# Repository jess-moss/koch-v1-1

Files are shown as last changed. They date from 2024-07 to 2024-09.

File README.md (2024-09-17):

# Low-Cost Robot Arm: Koch v1.1

This page contains the instructions to build a low-cost robot arm. It's an improved version of the original [Alexander Koch's robot](https://github.com/AlexanderKoch-Koch/low_cost_robot) to ease assembly. Thus, we call it Koch v1.1

For the curious reader, here are the most significant changes made:
1. Made small improvements to the hardware model including but not limited to: fixed screw interferences, cleaned up extraneous material, standardized hole sizes, removed screws fastening into plastic, added board platform to leader robot.
2. Added a platform for the leader arm. While not strictly necessary, this platform allows the follower arm to pick objects off the ground which it could not do in the previous configuration.
3. Removed the need for a soldering iron to assemble and for manually adjusting the voltage convertor, by replacing the DC convertor.
4. Added SolidWorks models to make it easier for the community to contribute.
5. Added a wiring diagram.
6. Added assembly video for leader and follower arm with SW animations.

## Assembly Instructions

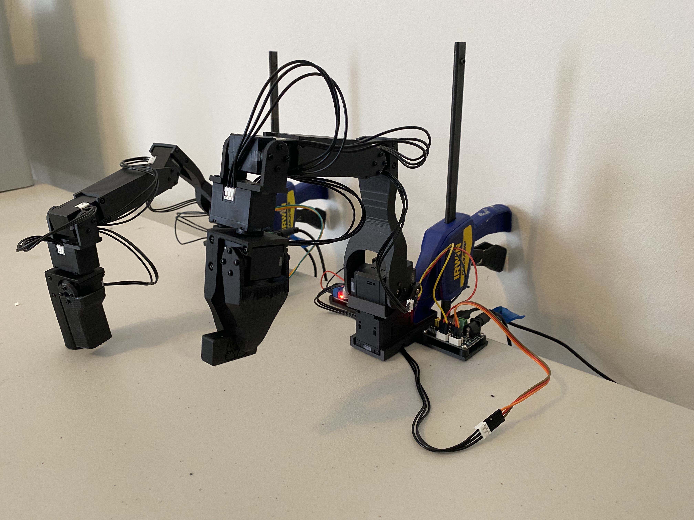
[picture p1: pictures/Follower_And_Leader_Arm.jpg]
Leader And Follower Arm


### Sourcing Parts
Order the off the shelf parts for the leader and follower arm using the links below. Note prices and items may vary slightly depending on geographic location.

#### Leader Arm

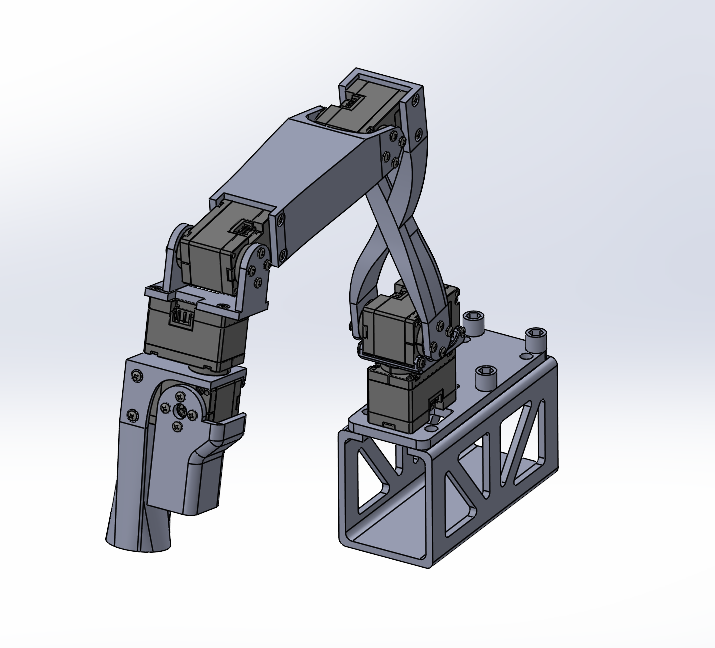
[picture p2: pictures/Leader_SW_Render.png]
Leader Arm


/!\ Warning: We only have links for US, EU, UK, China, and Japan for now. If you find links for other countries like India, please create an issue or PR so that we add them to the list.

| Part | Amount | Unit Cost (US) | Buy US | Unit Cost (EU) | Buy EU | Unit Cost (UK) | Buy UK | Unit Cost (RMB) | Buy CN | Unit Cost (JPY) | Buy JP |
|---|---|---|---|---|---|---|---|---|---|---|---|
| Dynamixel XL330-M077-T | 6 | $24 | [Robotis](https://www.robotis.us/dynamixel-xl330-m077-t) | 40€ | [MyBotShop](https://www.mybotshop.de/DYNAMIXEL-XL330-M077-T)-[GenRobots](https://www.generationrobots.com/en/403818-dynamixel-xl330-m077-t-servo-motor.html) | £27 | [RoboSavvy](https://robosavvy.co.uk/robotis-dynamixel-xl330-m077-t.html) | ¥255 | [TaoBao](https://item.taobao.com/item.htm?id=651202518645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.) | ¥4,070 | [Robotis](https://e-shop.robotis.co.jp/product.php?id=416) |
| XL330 Frame and Idler Wheel 4pcs set<sup>[1](#myfootnote1)</sup> |  1 | $10 | [Robotis](https://www.robotis.us/fpx330-h101-4pcs-set) | 12€ | [MyBotShop](https://www.mybotshop.de/DYNAMIXEL-FPX330-H101-4PCS-Set)-[GenRobots](https://www.generationrobots.com/en/403860-FPX330-H101-hinge-frame-and-idler-set-dynamixel-xl330.html) | £10 |  [RoboSavvy](https://robosavvy.co.uk/fpx330-h101-4pcs-set.html) | ¥100 | [TaoBao](https://item.taobao.com/item.htm?id=646782958666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..) | ¥2,024 | [Robotis](https://e-shop.robotis.co.jp/product.php?id=437) |
| Waveshare Serial Bus Servo Driver Board | 1 | $10 | [Amazon](https://a.co/d/7C3RUYU) | 6€ | [Eckstein](https://eckstein-shop.de/WaveShare-Serial-Bus-Servo-Driver-Board-for-ST-SC-Serial-Bus-Servos-EN) | £11 | [Amazon](https://www.amazon.co.uk/Waveshare-Integrates-Control-Applicable-Integrate/dp/B0CJ6TP3TP/)| ¥24 | [TaoBao](https://item.taobao.com/item.htm?id=739743280684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) | n/a | n/a |
| 5V Power Supply | 1 | $6 | [Amazon](https://a.co/d/5u90NVp) | 9€ | [Amazon](https://www.amazon.fr/LEYF-Alimentation-Universelle-Adaptateur-Enfichable/dp/B09NGVWBSY) | £10 | [Amazon](https://www.amazon.co.uk/Adapter-Switching-100-240V-5-5x2-1mm-Transformer-5V2A-UKCA/dp/B0CH6HFVTK/)| ¥10 | [TaoBao](https://detail.tmall.com/item.htm?id=662655385028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) | ¥899 | [Amazon](https://a.co/d/5u90NVp) |
| Jumper Wires 3*40 pcs set (M-M, M-F, F-F) | 1 | $7 | [Amazon](https://a.co/d/hQfk2cb) | 9€ | [Amazon](https://www.amazon.fr/dp/B0BRMKX5RT/) | £5 | [Amazon](https://www.amazon.co.uk/dp/B09KGRM98K/)| ¥10 | [TaoBao](https://detail.tmall.com/item.htm?id=608543275703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) | n/a | n/a |
| Table Clamp | 1 | $6 | [Amazon](https://a.co/d/4KEiYdV) | n/a | n/a | £14 | [Amazon](https://www.amazon.co.uk/BESSEY-TOOLS-CM30-Forged-C-Clamp/dp/B0006694I2/?th=1)| ¥8 | [TaoBao](https://detail.tmall.com/item.htm?id=597606333219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..) | n/a | n/a |
| Table Clamp 4pcs set<sup>[2](#myfootnote2)</sup> | 1 | n/a | n/a | 14€ | [Amazon](https://www.amazon.fr/CAUTIOUS-Serre-Joint-R%C3%A9glable-Serre-Joints/dp/B0CJMB3SKH) | n/a | n/a | n/a | n/a | n/a | n/a |
| 1.5mm Star/Cruciform Screwdriver 2pcs set | 1 |  $7 | [Amazon](https://www.amazon.com/HARFINGTON-Precision-Screwdriver-Eyeglasses-Electronic/dp/B0D3XQ97XM/?th=1)| 7€ | [Amazon](https://www.amazon.fr/sourcing-map-Cruciforme-%C3%89lectroniques-R%C3%A9paration/dp/B0BQ69J2QF) | £4 | [Amazon](https://www.amazon.co.uk/sourcing-map-Screwdriver-Eyeglasses-Electronics/dp/B0BLM2Y2Z5/) | ¥2 | [TaoBao](https://detail.tmall.com/item.htm?id=790258857614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) | n/a | n/a |
| USB C-A or C-C 2pcs set<sup>[3](#myfootnote3)</sup> | 1 | $9 | [Amazon](https://www.amazon.com/Charging-etguuds-Charger-Braided-Compatible/dp/B0B8NWLLW2/) | 8€ | [Amazon](https://www.amazon.fr/dp/B08J7PQGD7/) | £6 | [Amazon](https://www.amazon.co.uk/Anker-Charger-Braided-Standard-Charging/dp/B07DD5YHMH/)| ¥12 | [TaoBao](https://detail.tmall.com/item.htm?id=44425281296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) | n/a | n/a |
| Total | | $199 | | 305€ | | £222 | | ¥1696 | | ¥6993 | |

#### Follower Arm

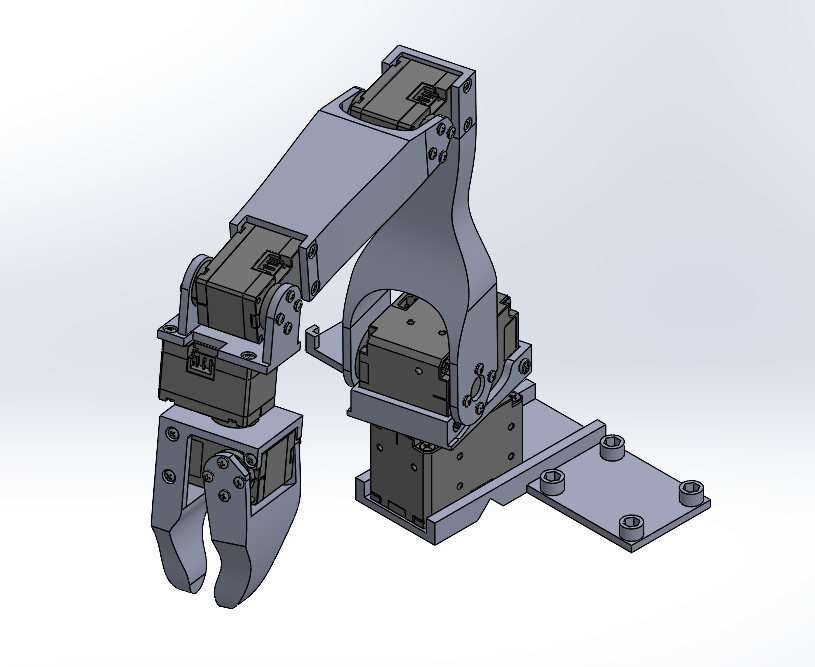
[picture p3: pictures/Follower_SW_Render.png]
Follower Arm


/!\ Warning: We only have links for US, EU, UK, China, and Japan for now. If you find links for other countries like India, please create an issue or PR so that we add them to the list.

| Part | Amount | Unit Cost (US) | Buy US | Unit Cost (EU) | Buy EU | Unit Cost (UK) | Buy UK | Unit Cost (RMB) | Buy CN | Unit Cost (JPY) | Buy JP
|---|---|---|---|---|---|---|---|---|---|---|---|
| Dynamixel XL430-W250-T |  2 | $50 | [Robotis](https://www.robotis.us/dynamixel-xl430-w250-t) | 57-61€ | [MyBotShop](https://www.mybotshop.de/DYNAMIXEL-XL430-W250-T)-[GenRobots](https://www.generationrobots.com/en/402823-dynamixel-xl430-w250-t-servomotor.html) | £47 | [RoboSavvy](https://robosavvy.co.uk/dynamixel-xl430-w250-t.html) | ¥485 | [TaoBao](https://item.taobao.com/item.htm?id=588178867677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) | ¥6,831 | [Robotis](https://e-shop.robotis.co.jp/product.php?id=40)
| Dynamixel XL330-M288-T |  4 | $24  | [Robotis](https://www.robotis.us/dynamixel-xl330-m288-t) | 40-46€ | [MyBotShop](https://www.mybotshop.de/DYNAMIXEL-XL330-M288-T)-[GenRobots](https://www.generationrobots.com/en/403817-dynamixel-xl330-m288-t-servo-motor.html) | £27 | [RoboSavvy](https://robosavvy.co.uk/robotis-dynamixel-xl330-m288-t.html) | ¥255 | [TaoBao](https://item.taobao.com/item.htm?id=648175925849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) | ¥4,070 | [Robotis](https://e-shop.robotis.co.jp/product.php?id=417)
| XL330 Frame and Idler Wheel 4pcs set<sup>[1](#myfootnote1)</sup> |  1 | $10 | [Robotis](https://www.robotis.us/fpx330-h101-4pcs-set) | 12€ | [MyBotShop](https://www.mybotshop.de/DYNAMIXEL-FPX330-H101-4PCS-Set)-[GenRobots](https://www.generationrobots.com/en/403860-FPX330-H101-hinge-frame-and-idler-set-dynamixel-xl330.html) | £10 |  [RoboSavvy](https://robosavvy.co.uk/fpx330-h101-4pcs-set.html) | ¥100 | [TaoBao](https://item.taobao.com/item.htm?id=646782958666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..) | ¥2,024 | [Robotis](https://e-shop.robotis.co.jp/product.php?id=437) |
| XL430 Idler Wheel set | 1 | $7 | [Robotis](https://www.robotis.us/hn11-i101-set) | 9€ | [MyBotShop](https://www.mybotshop.de/DYNAMIXEL-XL430-HN11-I101-Set)-[GenRobots](https://www.generationrobots.com/en/403206-hn11-i101-horn-set.html) | £7 | [Robosavvy](https://robosavvy.co.uk/hn11-i101-set.html)| ¥75 | [TaoBao](https://item.taobao.com/item.htm?id=581922883001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..) | ¥836 | [Robotis](https://e-shop.robotis.co.jp/product.php?id=147)
| Waveshare Serial Bus Servo Driver Board | 1 | $10 | [Amazon](https://a.co/d/7C3RUYU) | 6€ | [Eckstein](https://eckstein-shop.de/WaveShare-Serial-Bus-Servo-Driver-Board-for-ST-SC-Serial-Bus-Servos-EN) | £11 | [Amazon](https://www.amazon.co.uk/Waveshare-Integrates-Control-Applicable-Integrate/dp/B0CJ6TP3TP/)| ¥24 | [TaoBao](https://item.taobao.com/item.htm?id=739743280684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) | n/a | n/a |
| Voltage Reducer | 1 | $14 | [Amazon](https://www.amazon.com/EPLZON-Converter-5V-5-3V-Transformer-Regulator/dp/B09R4DBZJK) | 14€ | [Amazon](https://www.amazon.fr/dp/B0B58T2YY8/) | £15 | [Amazon](https://www.amazon.co.uk/Converter-Voltage-Regulator-Transformer-Charging/dp/B0989DKYWN) | ¥11 | [TaoBao](https://detail.tmall.com/item.htm?id=617425895508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) | n/a | n/a |
| 12V Power Supply | 1 | $12 | [Amazon](https://a.co/d/40o8uMN) | 15-36€ | [Amazon](https://www.amazon.fr/LEDMO-Alimentation-Adaptateur-Transformateurs-Chargeur/dp/B07PGLXK4X)-[GenRobots](https://www.generationrobots.com/en/400866-smps-charger-for-bioloid-and-dynamixel-robotis.html) | £13 | [Amazon](https://www.amazon.co.uk/Facmogu-Adapter-100-240V-Monitors-Amplifier/dp/B0CXPMJJMF/) | ¥20 | [TaoBao](https://detail.tmall.com/item.htm?id=678305663026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) | ¥1,685 | [Amazon](https://a.co/d/40o8uMN) |
| Jumper Wires 3*40 pcs set (M-M, M-F, F-F) | 1 | $7 | [Amazon](https://a.co/d/hQfk2cb) | 9€ | [Amazon](https://www.amazon.fr/dp/B0BRMKX5RT/) | £5 | [Amazon](https://www.amazon.co.uk/dp/B09KGRM98K/)| ¥10 | [TaoBao](https://detail.tmall.com/item.htm?id=608543275703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) | n/a | n/a |
| Table Clamp | 1 | $6 | [Amazon](https://a.co/d/4KEiYdV) | n/a | n/a | £14 | [Amazon](https://www.amazon.co.uk/BESSEY-TOOLS-CM30-Forged-C-Clamp/dp/B0006694I2/?th=1) | ¥8 | [TaoBao](https://detail.tmall.com/item.htm?id=597606333219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..) | n/a | n/a |
| Table Clamp 4pcs set<sup>[4](#myfootnote4)</sup> | 1 | n/a | n/a | 14€ | [Amazon](https://www.amazon.fr/CAUTIOUS-Serre-Joint-R%C3%A9glable-Serre-Joints/dp/B0CJMB3SKH) | n/a | n/a | n/a | n/a | n/a | n/a |
| 1.5mm Star/Cruciform Screwdriver 2pcs set<sup>[4](#myfootnote5)</sup> | 1 |  $7 | [Amazon](https://www.amazon.com/HARFINGTON-Precision-Screwdriver-Eyeglasses-Electronic/dp/B0D3XQ97XM/?th=1)| 7€ | [Amazon](https://www.amazon.fr/sourcing-map-Cruciforme-%C3%89lectroniques-R%C3%A9paration/dp/B0BQ69J2QF) | £4 | [Amazon](https://www.amazon.co.uk/sourcing-map-Screwdriver-Eyeglasses-Electronics/dp/B0BLM2Y2Z5/) | ¥2 | [TaoBao](https://detail.tmall.com/item.htm?id=790258857614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) | n/a | n/a |
| USB C-A or C-C 2pcs set<sup>[6](#myfootnote6)</sup> | 1 | $9 | [Amazon](https://www.amazon.com/Charging-etguuds-Charger-Braided-Compatible/dp/B0B8NWLLW2/) | 8€ | [Amazon](https://www.amazon.fr/dp/B08J7PQGD7/) | £6 | [Amazon](https://www.amazon.co.uk/Anker-Charger-Braided-Standard-Charging/dp/B07DD5YHMH/)| ¥12 | [TaoBao](https://detail.tmall.com/item.htm?id=44425281296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) | n/a | n/a |
| Total | | $278 | | 368€ | | £285 | | ¥2251 | | ¥15446 | |

### Printing the Parts
A variety of 3D printers are acceptable to print the parts necessary of the follower and leader arm. Follow the steps below to ensure a good print.

1. Choose a printer: When choosing a printer there are a variety of factors to consider. Below are the suggested printed settings, although using a printer outside these parameters may likely work as well.
   1. Precision: 0.2mm minimum height layer<sup>[7](#myfootnote7)</sup>
   2. Material: PLA+, ABS, PETG or other reasonably strong plastics.
   3. Nozzle Diameter: 0.4mm maximum nozzle diameter
   4. Infill Density: ~30% <sup>[8](#myfootnote8)</sup>
   5. Sample Printers: [Prusa Mini+](https://www.prusa3d.com/product/original-prusa-mini-semi-assembled-3d-printer-4/), [Bambu P1](https://us.store.bambulab.com/collections/p1-series/products/p1p), [Ender3](https://www.amazon.com/Comgrow-Creality-Ender-Aluminum-220x220x250mm/dp/B07BR3F9N6/), etc.  
2. Set up the printer
   1. Materials:<sup>[9](#myfootnote9)</sup>
      1. [Standard Glue Stick](https://www.amazon.com/Amazon-Basics-Washable-School-Sticks/dp/B0CRCWCGNW/)
      2. [Putty Knife](https://www.amazon.com/Warner-ProGrip-Putty-Knife-90133/dp/B000I1VEK6/)
   2. Setup and Takedown
      1. Ensure that the printer is calibrated and the bed level is correctly set using the printer specific instructions.
      2. Clean the print bed, making sure it is free from dust, or grease. If cleaning the bed using water, or other liquid, dry the bed.
      3. Use a standard glue stick and apply a thin, even layer of glue across the print area of the bed. Avoid clumping or uneven application.
      4. Load the printer filament using printer specific instructions.
      5. Ensure the printer settings match the ones suggested above (most printers have multiple settings so choose the ones that most closely match).
      6. Check file type, choose the file(s) from the hardware folder and print.<sup>[10](#myfootnote10)</sup>
3. Print one of each of parts found in `hardware/leader/STL` and `hardware/follower/STL`, which are listed below.
   1. Leader:
      1. Leader_Base
      2. Leader_Elbow_To_Wrist
      3. Leader_Elbow_To_Wrist_Extension
      4. Leader_Gripper_Handle
      5. Leader_Gripper_Trigger
      6. Leader_Shoulder_To_Elbow
      7. Leader_Platform<sup>[11](#myfootnote11)</sup>
      8. Robotis_FPX330_S101<sup>[12](#myfootnote12)</sup>
   2. Follower:
      1. Follower_Base
      2. Follower_Elbow_To_Wrist
      3. Follower_Elbow_To_Wrist_Extension
      4. Follower_Gripper_Moving_Part
      5. Follower_Gripper_Static_Part
      6. Follower_Shoulder_Rotation
      7. Follower_Shoulder_To_Elbow
   3. Optional Parts:<sup>[13](#myfootnote13)</sup>
      1. HuggingFace_Block
      2. LeRobot_Block
4. Take Down
   1. After the print is done, use the putty knife to scrape the the parts off the print bed.
   2. Remove any support material from parts.
   3. Reapply the glue stick before starting the next print.

### Assembling the Parts
Construct the leader and follower arms using the Assembly Video linked below. After you assemble the two arms from the video, power the leader arm using the 5V power supply<sup>[14](#myfootnote14)</sup>, and the follower arm using the 12V power supply. In addition, plug each arm into your computer using a USB-C cable.

Video of the Assembly: [Youtube](https://www.youtube.com/watch?v=8nQIg9BwwTk)

Note: The Leader Platform has been altered to be fastened instead of snapping into place, as the latter design was not creating a tight fit for certain printers. In time, this will be fixed in the video link above, but for now follow the below directions. 

Insert the nuts into the pockets on the underside of the Leader Platform. Then, use the M2x5 machine screws to fasten the Leader_Platform to the Leader_Base. You will need to temporarily remove the Waveshare Serial Bus Servo Driver Board to access the two fasteners beneath it.

Parts:
1. Leader_Platform
2. Four M2x5 Machine Screws
3. Four M2 Nuts

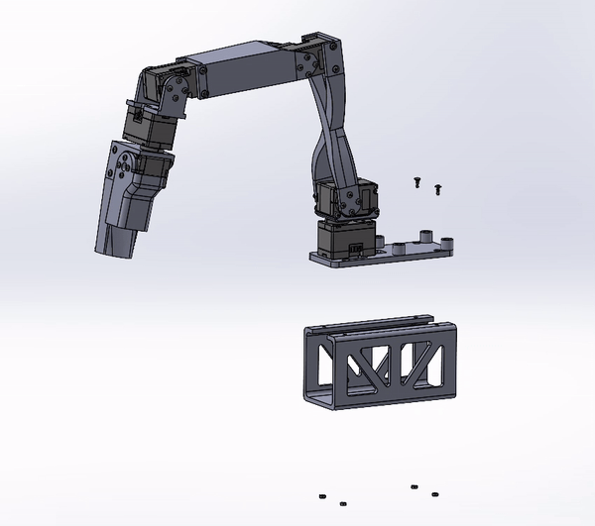
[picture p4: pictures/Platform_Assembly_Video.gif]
Platform Video


### Configure
While this robot can be programmed in a variety of manners, it is suggested to use with [LeRobot](https://github.com/huggingface/lerobot/blob/main/examples/7_get_started_with_real_robot.md).

### Footnotes
<a name="myfootnote1">1</a>: You will only use three idler wheels that come in this four piece set.\
<a name="myfootnote2">2</a>: You will only need one clamp in this four piece set.\
<a name="myfootnote3">3</a>: You will only need one chord in this two piece set. \
<a name="myfootnote4">4</a>: If you bought the 4 piece clamp set for the leader arm, you will not need to buy it again here, as only one clamp is necessary of the follower arm, and one for the leader arm.\
<a name="myfootnote5">5</a>: If you bought the screwdriver set for the leader arm, you will not need to buy it again here as the same screwdriver is used for the follower and leader arm.\
<a name="myfootnote6">6</a>: If you bought the two piece cable set for the leader arm, you will not need to buy it again here, as only one cable is necessary for the leader arm, and one for the follower arm. \
<a name="myfootnote7">7</a>: This precision is based on the fact the through holes for M2 fasteners are 2.4mm in diameter while the nominal diameter of a M2 fastener is 2mm. In a worst case scenario, this allows +/- 0.2mm while still allowing for screw alignment. However, if you are only capable of printing with a larger layer height, you will likely be fine, just ensure the screw holes align as expected.\
<a name="myfootnote8">8</a>: It is quite possible a lower density infill could be used, however, erring on the side of caution, I used 37% to ensure strong parts.  \
<a name="myfootnote9">9</a>: You do not need to buy these exact parts, but a glue stick and putty knife are almost always necessary for a good 3D print. The glue prevents parts from sticking to the print bed, and the putty knife helps scrape parts from the print bed. However, feel free to check with your specific printer instructions for if these parts are necessary. \
<a name="myfootnote10">10</a>: All the printers suggested will print STL files. However, if your printer only prints a different format, ensure you convert the file to the correct extension before printing. \
<a name="myfootnote11">11</a>: This is not strictly necessary to print but does allow the follower arm to reach the ground which is is otherwise unable to do in the current setup. \
<a name="myfootnote12">12</a>: You can either buy the Robotis [FPX330-S101](https://www.robotis.us/fpx330-s101-4pcs-set/), or 3D print it, but it is cheaper to print. \
<a name="myfootnote13">13</a>: Two blocks each the same size as a 2x4 Lego block, not necessary to print, but useful as a starting manipuland. \
<a name="myfootnote14">14</a>: The observant technician may realize the Serial Bus Servo Driver Board suggests an input DC voltage between 9 to 12.6V, where for the leader arm we are only applying 5V. This lower voltage will not hurt the board, and must be done to correctly power the servos on the leader arm.

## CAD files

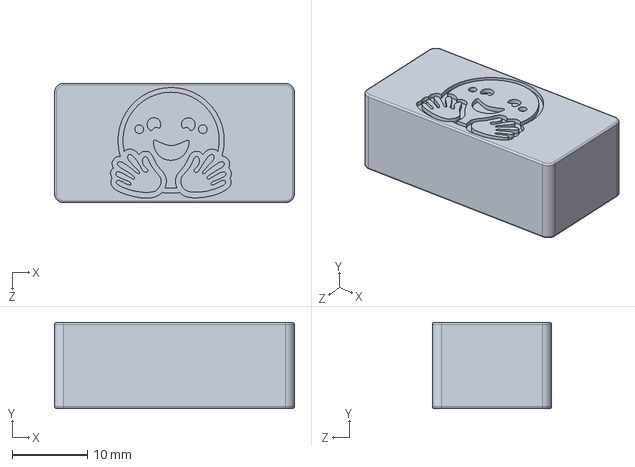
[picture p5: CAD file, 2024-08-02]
hardware/extras/SolidWorks/HuggingFace_Block.SLDPRT
31.8 x 11.4 x 15.8 mm

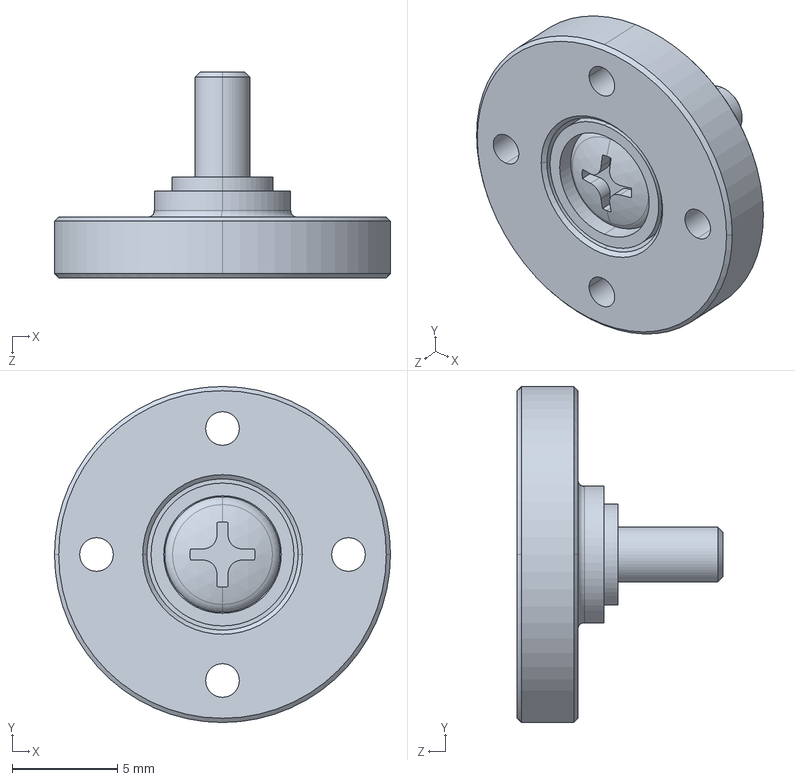
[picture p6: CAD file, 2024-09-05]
hardware/follower/STEP/Robotis_FPX330_H101.STEP
16.0 x 16.0 x 9.80 mm

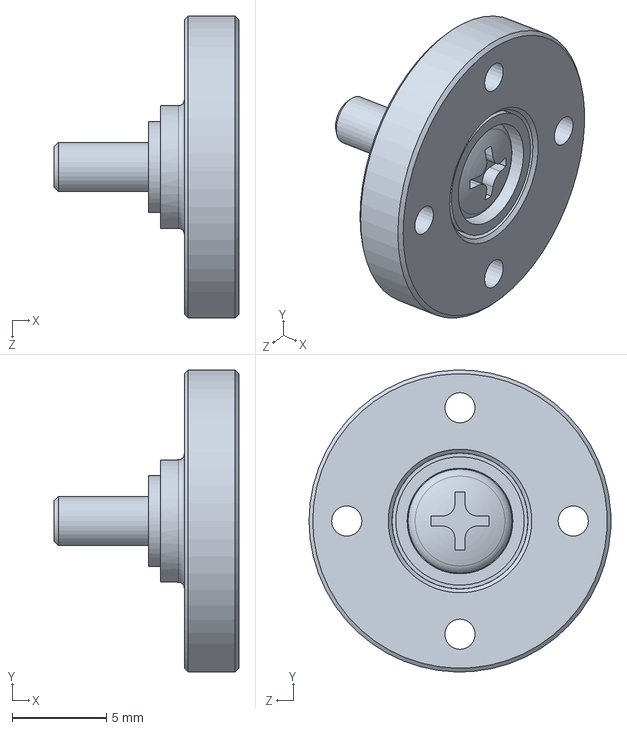
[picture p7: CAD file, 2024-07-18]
hardware/leader/SolidWorks/Robotis_FPX330_H101.SLDPRT
9.80 x 16.0 x 16.0 mm

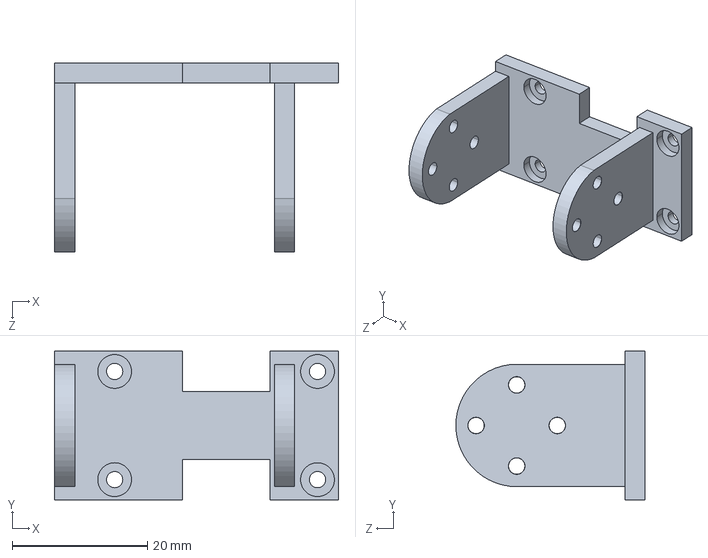
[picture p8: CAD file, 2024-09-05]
hardware/leader/STEP/Leader_Elbow_To_Wrist.STEP
42.0 x 22.0 x 28.0 mm

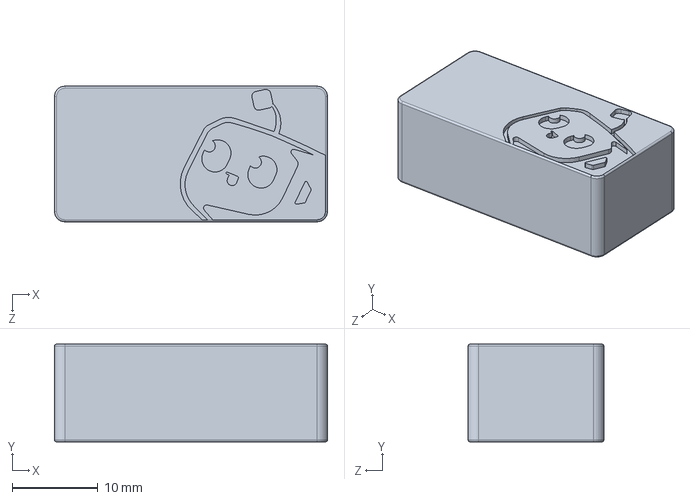
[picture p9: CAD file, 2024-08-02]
hardware/extras/SolidWorks/LeRobot_Block.SLDPRT
31.8 x 11.4 x 15.8 mm

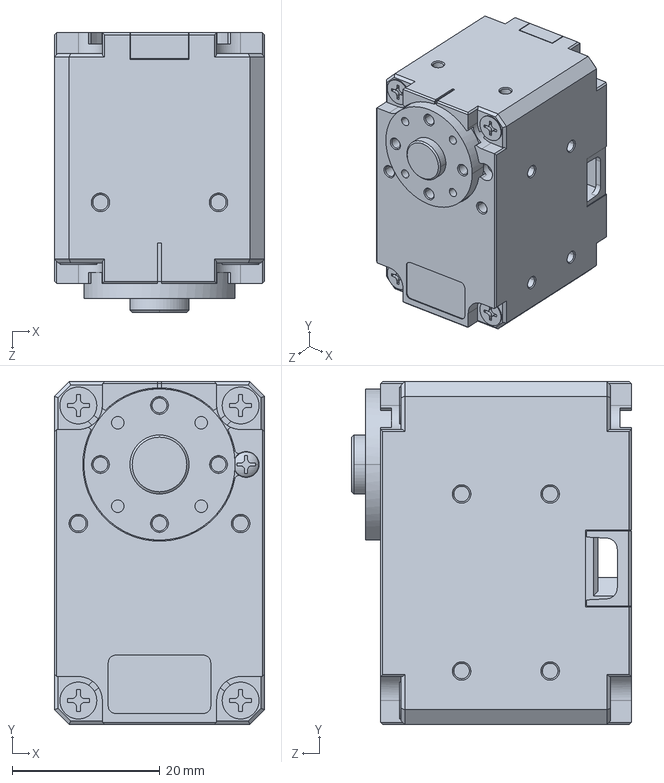
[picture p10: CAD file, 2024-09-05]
hardware/follower/STEP/Robotis_DYNAMIXEL_XL430_W250_T.STEP
28.5 x 46.5 x 37.9 mm

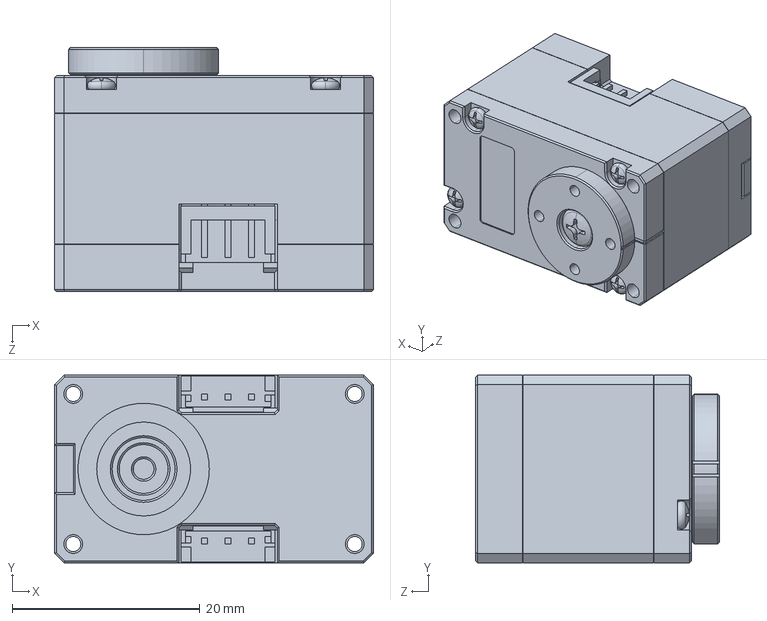
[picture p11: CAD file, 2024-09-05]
hardware/follower/STEP/Robotis_DYNAMIXEL_XL330_M288_T.STEP
34.0 x 20.0 x 26.0 mm

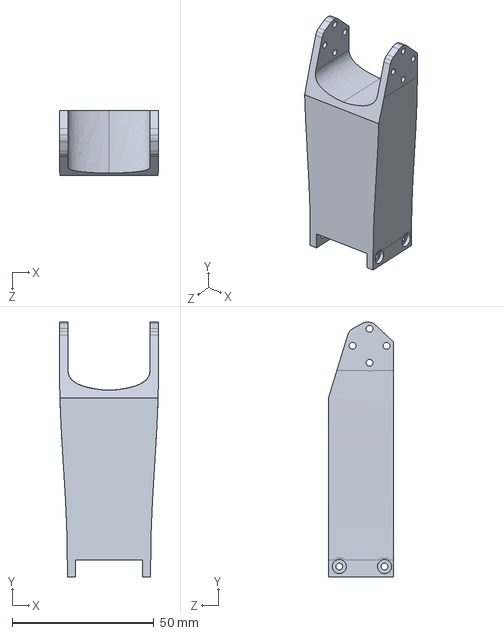
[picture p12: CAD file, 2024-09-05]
hardware/leader/STEP/Leader_Elbow_To_Wrist_Extension.STEP
35.0 x 90.1 x 23.0 mm

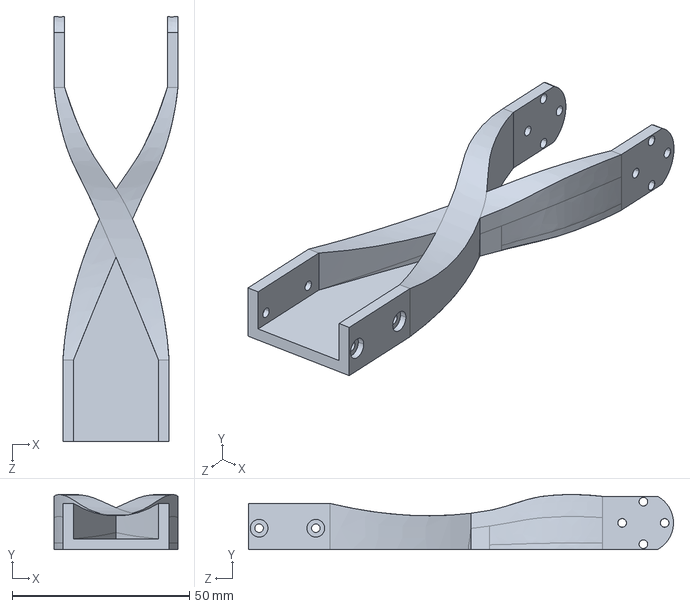
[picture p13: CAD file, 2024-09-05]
hardware/leader/STEP/Leader_Shoulder_To_Elbow.STEP
35.0 x 15.5 x 120.0 mm

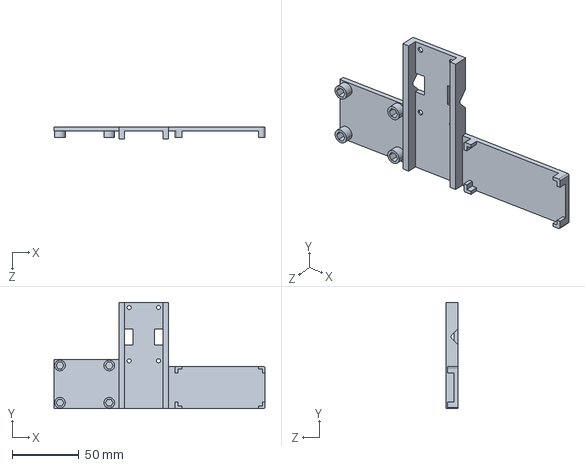
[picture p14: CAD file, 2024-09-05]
hardware/follower/STEP/Follower_Base.STEP
158.5 x 80.0 x 9.00 mm

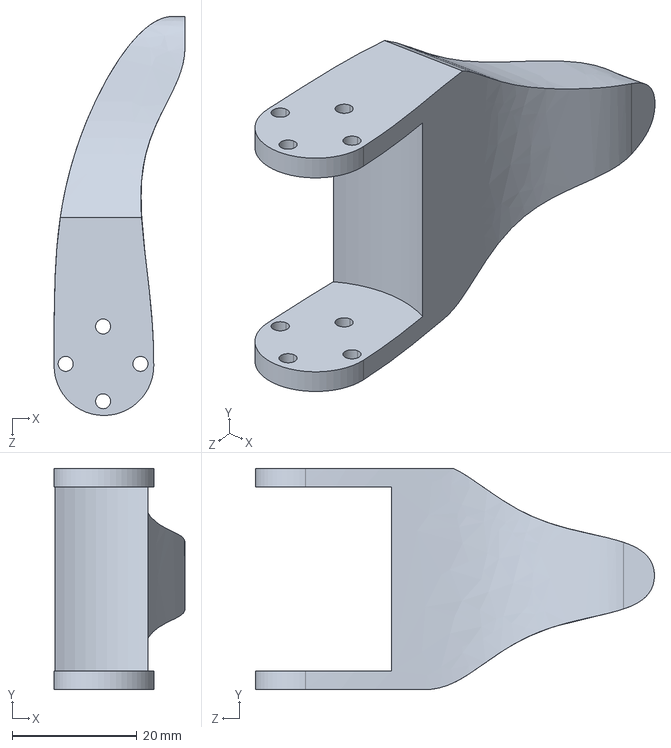
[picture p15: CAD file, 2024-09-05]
hardware/follower/STEP/Follower_Gripper_Moving_Part.STEP
21.0 x 35.5 x 64.0 mm

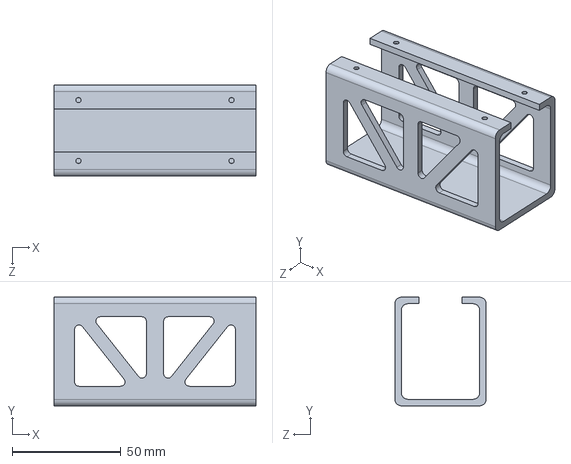
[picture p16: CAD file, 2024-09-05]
hardware/leader/STEP/Leader_Platform.STEP
93.0 x 50.0 x 42.0 mm

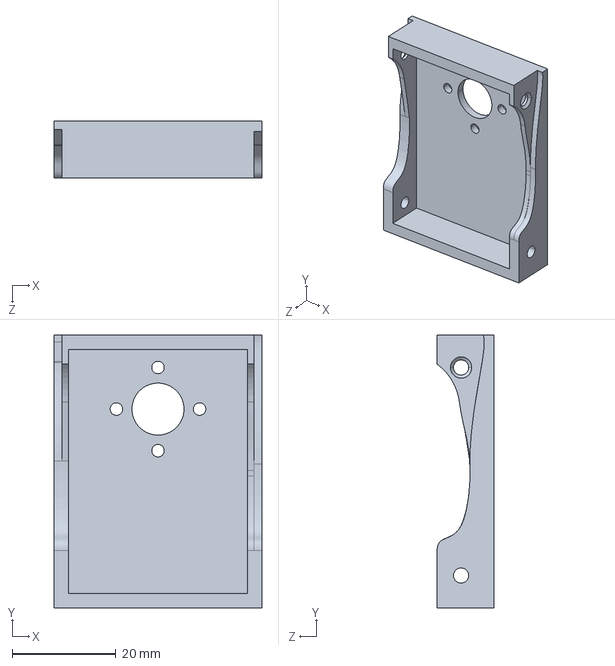
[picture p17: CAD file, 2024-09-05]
hardware/follower/STEP/Follower_Shoulder_Rotation.STEP
40.0 x 52.5 x 10.9 mm

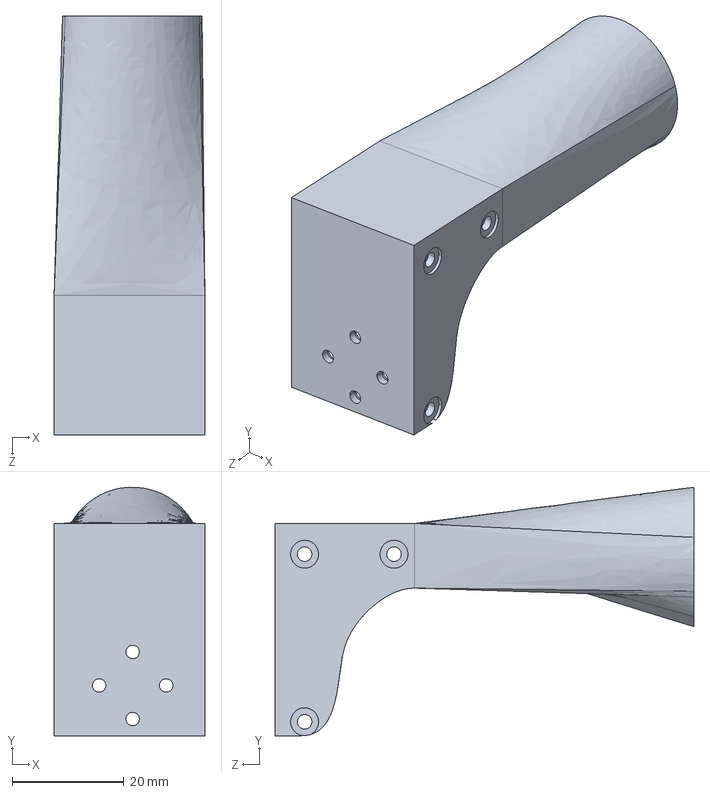
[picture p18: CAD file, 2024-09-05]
hardware/leader/STEP/Leader_Gripper_Handle.STEP
27.0 x 44.5 x 75.0 mm

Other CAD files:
hardware/leader/STEP/Leader_Arm.STEP
hardware/follower/STEP/Follower_Arm.STEP
hardware/leader/STEP/Leader_Robotis_FPX330_H101.STEP
hardware/follower/STEP/Follower_Elbow_To_Wrist.STEP
hardware/extras/STL/HuggingFace_Block.STL
hardware/extras/STL/LeRobot_Block.STL
hardware/follower/STEP/Follower_Elbow_To_Wrist_Extension.STEP
hardware/follower/STEP/Follower_Gripper_Static_Part.STEP
hardware/follower/STEP/Follower_Shoulder_To_Elbow.STEP
hardware/follower/STEP/Robotis_DYNAMIXEL_XL430_Spacer.STEP
hardware/follower/STEP/Robotis_HN11_I101.STEP
hardware/follower/STL/Follower_Base.STL
hardware/follower/STL/Follower_Elbow_To_Wrist.STL
hardware/follower/STL/Follower_Elbow_To_Wrist_Extension.STL
hardware/follower/STL/Follower_Gripper_Moving_Part.STL
hardware/follower/STL/Follower_Gripper_Static_Part.STL
hardware/follower/STL/Follower_Shoulder_Rotation.STL
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

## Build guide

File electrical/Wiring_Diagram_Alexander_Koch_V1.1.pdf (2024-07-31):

A | A
B | B
C | C
D | D

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
## TITLE:

Alexander Koch Robot Arm Wiring Diagram V1.1 | REV: 1.0
Date: | 2024-07-08

## Sheet: 1/1 Drawn By: Jess Moss

## Company: Hugging Face

B0CTMM4LWK

SERVO_DRIVER_BOARD

V

12V
G

GND

D

DATA
V

12V
G

GND

12V | PWR
Connect To Computer | USB

D

DATA

Robot Cable-X3P 180mm

MOTOR_CABLE

12V 2
GND 1

DATA 3

902-0135-000

DYNAMIXELXL430-W250-T

Plug 2

Plug 1

902-0135-000

DYNAMIXELXL430-W250-T

Plug 2

Plug 1

DATA 3
5V 2
GND 1

902-0163-000

DYNAMIXELXL330-M288-T

Plug 2

Plug 1

902-0163-000

DYNAMIXELXL330-M288-T

Plug 2

Plug 1

902-0163-000

DYNAMIXELXL330-M288-T

Plug 2

Plug 1

902-0163-000

DYNAMIXELXL330-M288-T

Plug 2

Plug 1

# Follower Arm:

# Leader Arm:

B0CTMM4LWK

SERVO_DRIVER_BOARD

V

5V
G

GND

D

DATA
V

5V
G

GND

5V | PWR
Connect To Computer | USB

D

DATA

Robot Cable-X3P 180mm

MOTOR_CABLE

5V 2
GND 1

DATA 3

902-0162-000

DYNAMIXELXL330-M077-T

Plug 2

Plug 1

902-0162-000

DYNAMIXELXL330-M077-T

Plug 2

Plug 1

902-0162-000

DYNAMIXELXL330-M077-T

Plug 2

Plug 1

902-0162-000

DYNAMIXELXL330-M077-T

Plug 2

Plug 1

902-0162-000

DYNAMIXELXL330-M077-T

Plug 2

Plug 1

902-0162-000

DYNAMIXELXL330-M077-T

Plug 2

Plug 1

EP-JY-DC5

VOLTAGE_REDUCER
GND IN-

OUT+ 5V
OUT- GND

12V IN+

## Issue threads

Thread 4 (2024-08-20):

minimum area needed to use both leader and follower arms together

ramkumarkoppu, 2024-08-20:
Hi,

May I know what is minimum table area needed to use both leader and follower arms together in space constrain lab environment?

jess-moss, 2024-08-20:
It really depends on what you are trying to do, I currently have both my arms together in a 1ft x 1ft square for testing. You could probably squeeze this even tighter if need be.

Closed 2024-08-22.

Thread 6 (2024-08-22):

solidworks file format

Kevin-spark, 2024-08-22:
Thank you for your excellent work. When I tried to open the project's SolidWorks files, I received a version mismatch warning. Could you please let me know which version of SolidWorks you are using? Also, would it be possible to save the files in STEP format? The STP format is more universally compatible for 3D CAD file exchange.

I would greatly appreciate it if you could assist with this. Thank you!

jess-moss, 2024-08-22:
I am using SolidWorks 2024.

I can definitely save a STEP version but it will take a few days. In the meantime hopefully you can at least use the STL files (which you can also open with SW).

Hope this helps!

haoyangli16, 2024-09-04:
Hi @jess-moss ,

Really a nice and useful work! But could you please save the SolidWorks files in an earlier version? Many engineers, including myself, aren't using the latest version. Alternatively, providing a STEP file would make it even more accessible across different software.

Thanks so much for your consideration and for the great work!

jess-moss, 2024-09-04:
Hello @haoyangli16-- thank you so much! What version of SW do you recommend? I can pretty easily save these files as SW22 or  SW23. Would that be sufficient? In addition, it is on my list to save them as a step file- I just have not gotten around to it yet. Since a few people have asked, I will try and do that by the end of the week. Thank you!

jess-moss, 2024-09-05:
@haoyangli16 @Kevin-spark just added the step files. Hope this helps!

Closed 2024-12-05.

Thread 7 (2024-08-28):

How should I assemble this in China?

Jerry-155, 2024-08-28:
I would like to know where in China I can source these parts and assemble a robotic arm, or just buy a finished product that can be plugged into the lerobot.tanks

CHANGgreenEVER, 2024-08-31:
Same problem

Felix-Zhenghao, 2024-09-01:
Hi, I have bought all stuff from TaoBao and I will send a PR perhaps today or tomorrow.

Hezhexi2002, 2024-09-01:
> Hi, I have bought all stuff from TaoBao and I will send a PR perhaps today or tomorrow.

Wonderful work!I'd like to build one arm following your sheet after I finish the exam!

Closed 2024-09-02.

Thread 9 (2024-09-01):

How can I assemble it in India?

Harshit0143, 2024-09-01:
Please make a links for assembling it in India too!

dsriaditya999, 2024-09-23:
I am also waiting for it!

jess-moss, 2024-12-05:
Issue #22 actually has the links! Still hope someone creates a PR with these so I can merge it!

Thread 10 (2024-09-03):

This is Amazing, Thank You!

MichaelrMentele, 2024-09-03:
Thank you for putting this together, the original instructions were difficult (though still much appreciated!) and this is a great improvement, thanks @jess-moss! 🙏 ❤️

jess-moss, 2024-09-03:
Of course! Glad it has been helpful so far! :tada:

Closed 2024-09-03.

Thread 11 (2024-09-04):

FPX330-S101  or FPX330-H101

MichielBbal, 2024-09-04:
In your YouTube video (https://www.youtube.com/watch?v=8nQIg9BwwTk) I see you use the FPX330-S101. While in the 'sourcing parts' you mention FPX330-H101. Which one should we use? Thank you.

jess-moss, 2024-09-04:
Per the BoM You will need FPX330-H101. You can either 3D print or buy FPX330-S101 as well (see footnote 12). Let me know if this is still not clear.

MichielBbal, 2024-09-05:
Thanks. All clear, was lucky to have some old M2's laying around.

Closed 2024-09-05.

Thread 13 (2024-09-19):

Cannot update firmware on XL-430 via waveshare servo driver

codenamev, 2024-09-19:
Hey there!  Firstly, thank you for an awesome project ❤️

I was able to fully assemble everything and ran a successful teleoperation as part of [the LeRobot calibration step](https://github.com/huggingface/lerobot/blob/main/examples/7_get_started_with_real_robot.md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).  However, when it came time to [run it with cameras enabled](https://github.com/huggingface/lerobot/blob/main/examples/7_get_started_with_real_robot.md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), the arm swung up and the top XL-430 started flashing red.  After that, I verified all the connections and proper voltage, but was unable to recalibrate these.

I thought it could be a firmware issue, and downloaded [the Dynamixel Wizard](https://emanual.robotis.com/docs/en/software/dynamixel/dynamixel_wizard2/).  Unfortunately, [there are known issues updating the firmware over USB-C with the Waveshare servo driver](https://forum.robotis.com/t/firmware-transfer-failed-on-new-motor/5819/18).  I ordered their [official U2D2](https://www.robotis.us/u2d2/) (coming today) and will update this to see if that resolves the issue, but wanted to create this in case others have issues (might be worth a mention in the README).

PradeepKadubandi, 2024-11-28:
Just to add my experience, I had the same trouble using Mac / Windows software. But when I tried it on Linux, I was able to use the same board to recover the firmware.

I second the "awesome" comment! Thank you LeRobot team and @jess-moss . This repository is much more detailed and helpful to be able to assemble and use these arms.

jess-moss, 2024-12-05:
Thank you so much!!

That is an interesting thought. I know the Waveshare boards do commonly have some issues and are definitely not as robust as the official Robotis board so that is a good step. I personally use linux and did not encounter problems updating but will keep this issue open so others are aware.

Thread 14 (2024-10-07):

Leader arm base is different on video x github

diegoakel, 2024-10-07:
This base:

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

Is different from the one on the hardware/leader folder.

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

includingThis, 2024-10-27:
We had no issues assembling the parts nevertheless. However, in the video the servo is placed in a position turned 90 degrees. May be related to different base layout. Drawing in the manual confirms correct servo position parallel to the long side of the base.

diegoakel, 2024-10-27:
Yes, not a real problem to be honest. Maybe just a version difference between video and repo. I guess this issue could be closed.

Closed 2024-10-28.

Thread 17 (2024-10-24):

Required printed 3 parts supplier?

ricardok1, 2024-10-24:
Hi there

Can someone suggest how to buy the parts that require 3d printing?

Thanks
Ricardo

diegoakel, 2024-10-28:
You should look for some print farm that is located close to you. [PCBway ](https://www.pcbway.com/rapid-prototyping/3d-printing/) for example.

Closed 2024-11-02.

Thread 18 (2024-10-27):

Plug 1 / plug 2 on the servos, does it matter?

includingThis, 2024-10-27:
How to distinguish plug 1 from plug 2 on the hardware? Or is this irrelevant?
We don't want to break the dynamixels and are unsure whether we can put the cables in either of the two plugs of the servos?

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

diegoakel, 2024-10-28:
this is irrelevant

includingThis, 2024-10-29:
Great, thanks!

Closed 2024-10-29.

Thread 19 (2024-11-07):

Upload STL/STEP file of assembled koch-v1-1

Quest2GM, 2024-11-07:
Hi @jess-moss,

Thank you for this repository! I'm wondering if its possible to upload the STL/STEP file of the fully assembled leader/follower arm. I am trying to get the DH parameters of the manipulators and it would be useful to have the STL/STEP file so that the numbers can be computed more accurately.

Thanks!

Closed 2025-03-19.

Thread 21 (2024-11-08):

assembly instructions

eyast, 2024-11-08:
Thanks for this amazing repo. A small suggestion would be to provide the assembly instructions as a set of "Ikea-like" ones (without the video, simply sequential 3d renders that show which part goes where. i.e. like this, one after the other on the README page.. it would make assembling a lot easier I believe.

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

jess-moss, 2024-12-05:
@eyast That is a great suggestion! Someone in the open source community started to do this I believe! If someone from open source does it I would happily add it to the repo but unfortunately I likely won't get to it for a while! Thank you!

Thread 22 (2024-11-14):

Robot Part List Links in India

metaseeker1, 2024-11-14:
1. https://www.thingbits.in/products/xl430-w250-t-dynamixel-smart-servo-motor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
2. https://www.mgsuperlabs.co.in/estore/XL-330-M-288-T
3. https://www.mgsuperlabs.co.in/estore/FPX330-H101-4pcs-Set
4. https://mgsuperlabs.in/robotics/robotis/8045/hn11-i101-set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
5. https://thinkrobotics.com/products/serial-bus-servo-driver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
6. https://www.amazon.in/REES52-Converter-Regulator-Inverter-Transformer/dp/B07LCNQKHP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
7. https://www.amazon.in/Taapsee-Adapter-Mounted-Converter-Transformer/dp/B0CTG66MR3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
8. https://www.amazon.in/IEIDidacticsTM-Jumper-Wires-Female-jumper/dp/B099R6HS7M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
9. https://www.amazon.in/Homdum%C2%AE-Heavy-Clamp-Clamping-Pieces/dp/B081K3DMBD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
10. https://www.amazon.in/HARFINGTON-Precision-Screwdriver-Eyeglasses-Electronic/dp/B0D3TFWKML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
11. https://www.amazon.in/Wayona-Nylon-Braided-Charger-Wc10Cb1/dp/B07F1K736H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

jess-moss, 2024-12-05:
Hello, thank you so much for these links! If you (or someone else creates a PR with these part links I will merge it)!

Thanks again!

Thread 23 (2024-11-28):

With Follower arm, I was able to detect only the big motors and not the smaller chain?

PradeepKadubandi, 2024-11-28:
Thanks to LeRobot updates to Koch arm (this repository), I was able to assemble and figure out a lot of issues along the way.

I am still stuck here and wondering if anyone has any insight (this is not really an issue with the current repository though).

I did all the wiring and connections (double / triple checked) but when I connect the follower arm with 12V power (I am using the soldered version of voltage reducer to be clear - not the koch v1 voltage reducer), I am only seeing the 2 big motors in scan and not others.

I did quite a few debugging:
- Used 5V power to test the 4 small motor series and was able to detect them in scan (eliminates the issues with motors)
- Individually connected each motor through 12V power and my voltage reducer (using the follower arm) - this eliminated that there is an issue with voltage reducer or the servo board itself.

But when I connected both motor groups using the 12V power, somehow only detecting the 2 big ones and not the 4 smaller chain. Anyone faced a similar issue? Any insights on what could I try?

PradeepKadubandi, 2024-11-30:
Hmm, what made the above go away is switching the bigger motor chain port and smaller motor chain port on servo board. It appears to me that this detail of electrical diagram is also important.

The DVG slot closer to the power on servo board should be connected to the 4 motor chain of small motors. The other DVG slot in between power and USB must be connected to 2 motor chain of bigger motors. Then only all 6 of them were detected.

If I do it the other way around, only 2 bigger motors are being detected.

That's my observation. If someone observes anything else (that switching would still make the 6 motors detectable) I would love to know.

Also, if some electrical/hardware person validates/refutes my hypothesis that the exact positions of DVG slots matter (based on their understanding of servo board), I'd love to know that too!

Closed 2024-11-30.

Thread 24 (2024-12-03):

The leader platform looks different in assembly video compared to STL

PradeepKadubandi, 2024-12-03:
Thank you for this repository! This has been super helpful for assembly and parts. The wiring instructions, assembly videos everything is great.

One small detail - I see the STL for Leader Platform looks different compared to what I see in the assembly video. The one in assembly video seems simpler and more convenient where the STL is still tightened with screws. Is my understanding correct? Am I missing something? (Attaching the screenshot from assembly video)
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

PradeepKadubandi, 2024-12-03:
This is the platform STL currently in the repository: https://github.com/jess-moss/koch-v1-1/blob/main/hardware/leader/STL/Leader_Platform.STL . Looks like this:

Closed 2025-07-15.

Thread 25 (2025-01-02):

I am new to this great project and hardware. Where to find the firmware code? I mean, The code and IDE for the Servo Driver Board.

guotong1988, 2025-01-02:
Thank you very much!

I mean, how to get started with the Servo Driver Board?

guotong1988, 2025-01-03:
https://www.waveshare.net/wiki/Bus_Servo_Adapter_(A)_

guotong1988, 2025-01-03:
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
PC as example for USB connection.

Closed 2025-01-03.

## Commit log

2024-07-18 Added SW, STL and README. NEeds some small edits
    [Follower_Arm.SLDASM, Follower_Base.SLDPRT, Follower_Base.STL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]
2024-07-19 Altered Leader elbow to wrist extension to have M2 thru holes.
    [Leader_Arm.SLDASM, Leader_Elbow_To_Wrist_Extension.SLDPRT]
2024-07-19 Adding STL file for FPX frame.
    [Robotis_FPX330_S101.STL]
2024-07-23 new assembly video and leader base.
    [Leader_Base.STL]
2024-07-31 Added wiring diagram.
2024-08-01 Needed to alter counterbores
    for increased thread engagement.
    [Leader_Base.SLDPRT]
2024-08-01 Needed to increase depth of counterbore
    for appropriate thread engagement.
    [Leader_Base.STL]
2024-08-01 Added Blocks To Print
    If you don't have Legos and want something to pick up, consider printing these cute HF and LeRobot branded Lego sized blocks.
    [HuggingFace_Block.SLDPRT, LeRobot_Block.SLDPRT]
2024-08-01 Added Blocks
    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
    [HuggingFace_Block.STL, LeRobot_Block.STL]
2024-08-02 Material was too thin on standoffs
    so when you pulled out support material it would break through depending on your printer.
    [Leader_Base.SLDPRT]
2024-08-02 Material was too thin on standoffs
    so when you removed support material, it would break through.
    [Leader_Base.STL]
2024-08-02 Changed Block Size to Lego 2x4 Size
    [HuggingFace_Block.SLDPRT, LeRobot_Block.SLDPRT]
2024-08-02 Changed block size to size of a 2x4 Lego Block
    [HuggingFace_Block.STL, LeRobot_Block.STL]
2024-08-08 Added correct Youtube assembly video link
2024-08-08 changed orientation of block
    [HuggingFace_Block.STL, LeRobot_Block.STL]
2024-08-08 Changed orientation of HF block.
    [HuggingFace_Block.STL]
2024-08-08 Fixed orientation of STL files.
    [Follower_Gripper_Moving_Part.STL, Follower_Gripper_Static_Part.STL, Follower_Shoulder_To_Elbow.STL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]
2024-08-13 Fixed BoM for UK Parts.
2024-08-29 Changed the leader platform design to include fasteners as the snap into place design was not providing a tight fit for certain printers, and provided documentation to do this. Also, made small chang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
    [Follower_Arm.SLDASM, Follower_Gripper_Moving_Part.SLDPRT, Follower_Gripper_Moving_Part.STL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]
2024-09-01 Add links to assemble koch v1.1 in China
2024-09-05 Added step files for the follower and leader arm.
    [Follower_Arm.STEP, Follower_Base.STEP, Follower_Elbow_To_Wrist.STEP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]
